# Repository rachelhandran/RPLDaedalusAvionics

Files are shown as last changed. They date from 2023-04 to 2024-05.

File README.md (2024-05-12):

# RPL Daedalus Avionics

5.11.24
Welcome! This is my guide for the RPL Daedalus Project Avionics, in particular, the software and PCB files I designed and used on my rocket during the 2022-2023 cohort.
I used an Arduino Nano to drive 2 sensors, a pressure/altitude/temperature sensor (BMP388), and an IMU/gyroscope/accelerometer/magnetometer (BNO055). The system also includes an SD Card and Module, and a battery. The code written is designed to read pressure/temp/altitude, IMU data, and write it to the SD Card.

The PCB Files are attached, I designed in Eagle. Feel free to copy and edit these files to add or remove any functionalities.

See my latest version and updates below.

## v2/IMUFlightComp.ino
5.20.23 

This is the newest flight computer software that interfaces with the PCB v2.0. It has support for BMP388 temperature, pressure, and altitude sensing, as well as IMU 9DoF Raw Data: Accelerometer, Gyroscope, and Magnetometer data. The software reads all the above data, including IMU calibration status data, and writes them to the SD card in CSV format.

CSV format:
*Temperature (C), Pressure (hPa), Altitude (m), IMU Calibration (System), IMU Calibration (Accelerometer), IMU Calibration (Gyroscope), IMU Calibration (Magnetometer), Accel_X (m/s^2), Accel_Y (m/s^2), Accel_Z (m/s^2), Gyro_X (rad/s), Gyro_Y (rad/s), Gyro_Z(rad/s), Mag_X (uT), Mag_Y (uT), Mag_Z (uT)*

This version of code also supports a Piezo buzzer (but the PCB does not have a spot for the buzzer, this code can only be used on a system designed with a buzzer.) This version plays a constant buzz to inform that data is successfully reading and writing to SD. If not buzzing, the SD Card is likely not initialized properly. Eject and re-enter, and click RESET on the Arduino. Continue until the buzz begins.

## Hardware Setup
5.21.23
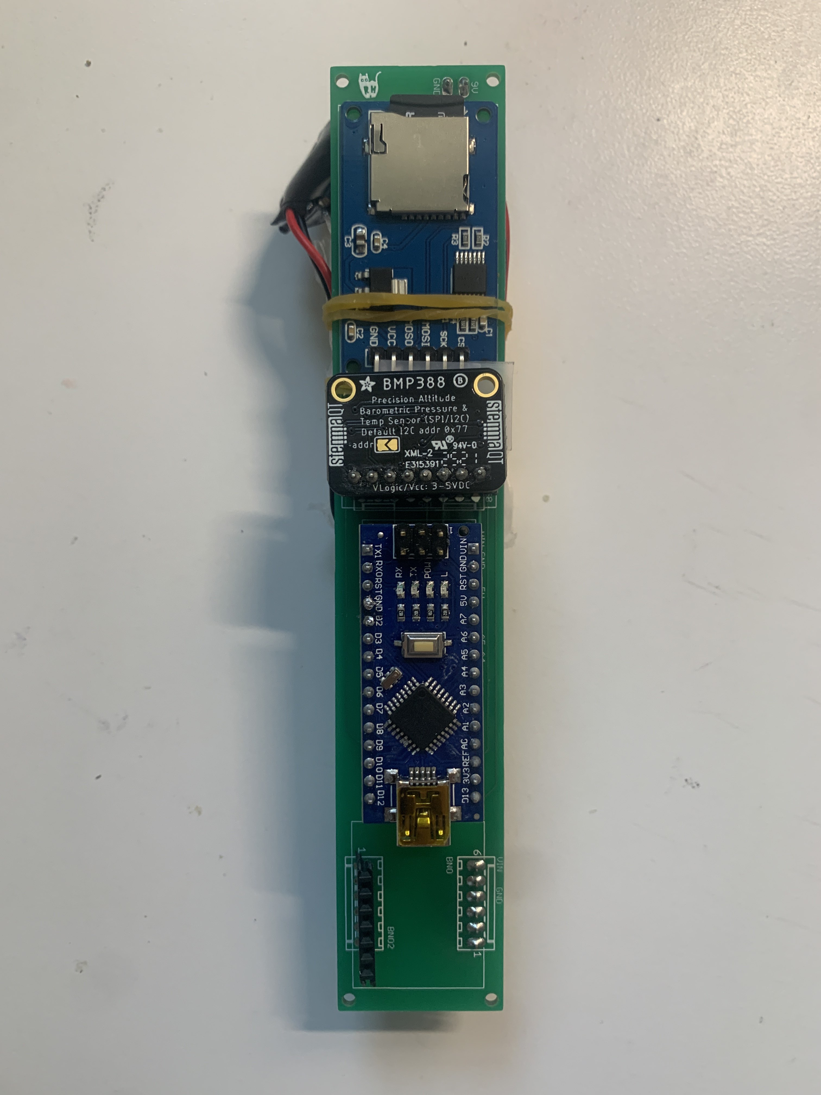
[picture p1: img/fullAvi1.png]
front

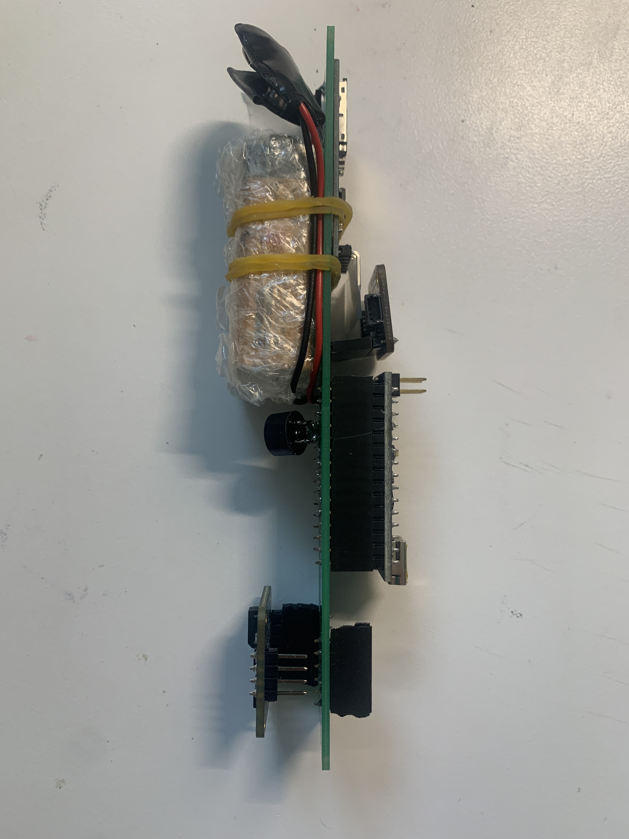
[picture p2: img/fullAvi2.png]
side

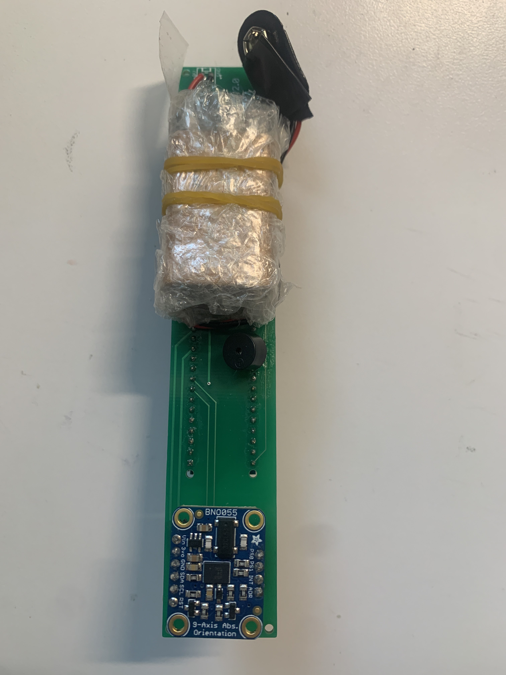
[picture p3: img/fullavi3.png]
back

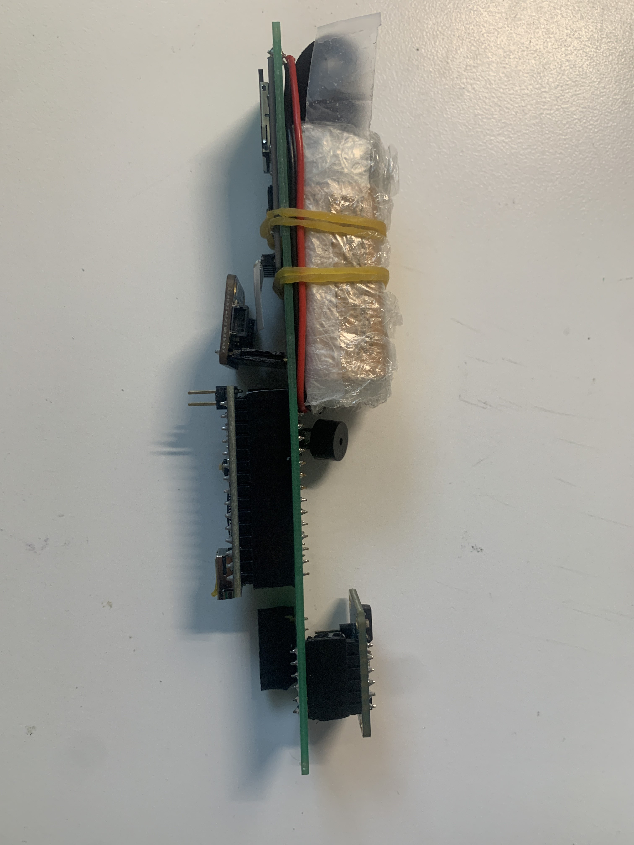
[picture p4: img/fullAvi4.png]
other side


## PCB v2.0
5.6.23

3D Views:
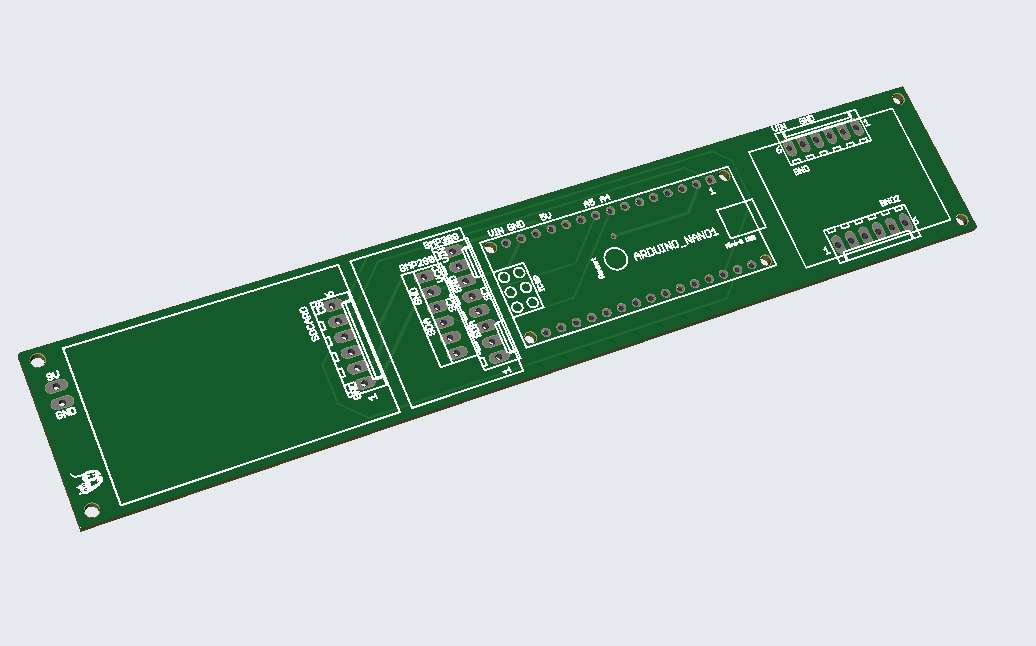
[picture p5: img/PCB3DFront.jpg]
3D Front View

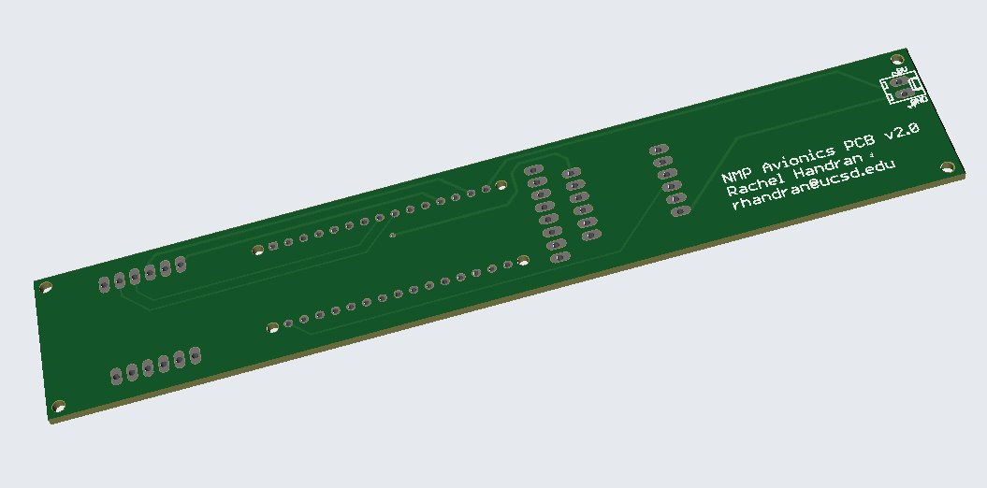
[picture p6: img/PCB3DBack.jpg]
3D Back View


Board: 
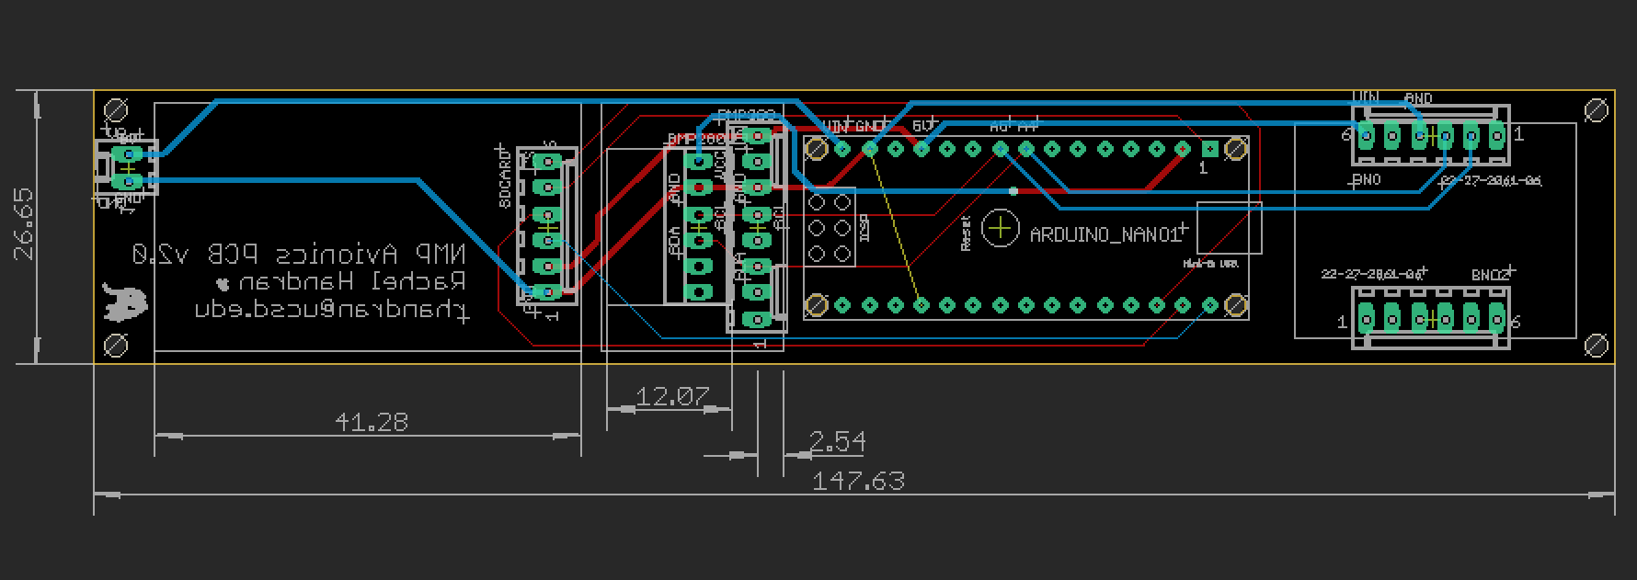
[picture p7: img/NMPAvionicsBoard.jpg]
Board

Schematic: 
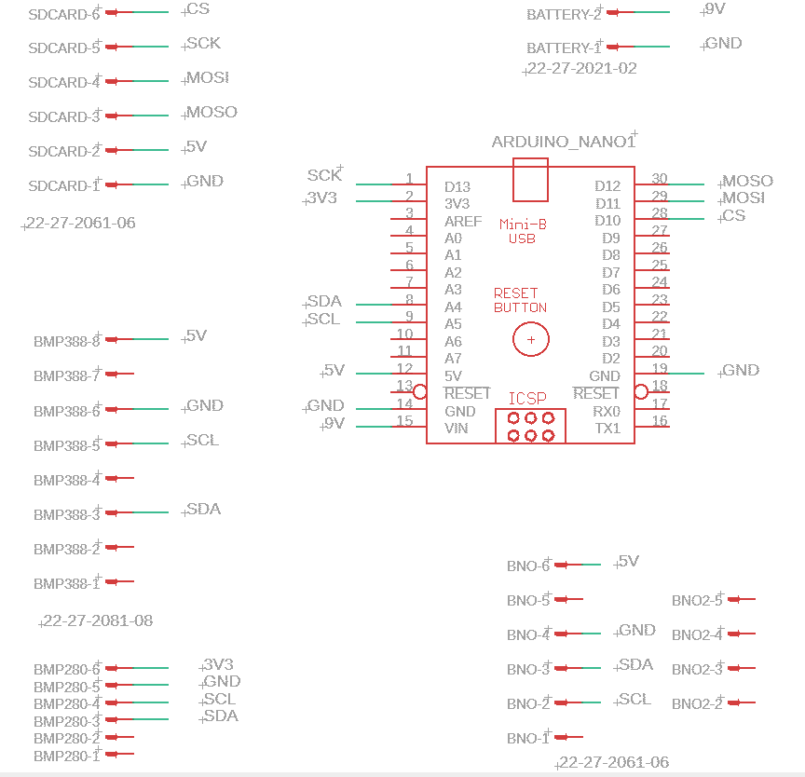
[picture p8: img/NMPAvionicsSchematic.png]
Schematic


## v1.0

This is the flight computer for our NMP Avionics system. 

*The software is designed for BMP388 only. Software is not necessarily compatible for BMP280. Hardware IS compatible with both, but you must write your own code to call the BMP280 library instead of the BMP388.*

`flightComputer.ino` is the flight program. Once uploaded, there will be a 5s delay, then the BMP388 sensor will read in temp, pressure, and altitude data, and write to a file in the SD card once every 100ms.

`flightCompDebug.ino` is outdated. It was a duplicate sandbox code to practice and debug. 

### Hardware/PCB v1 Setup:
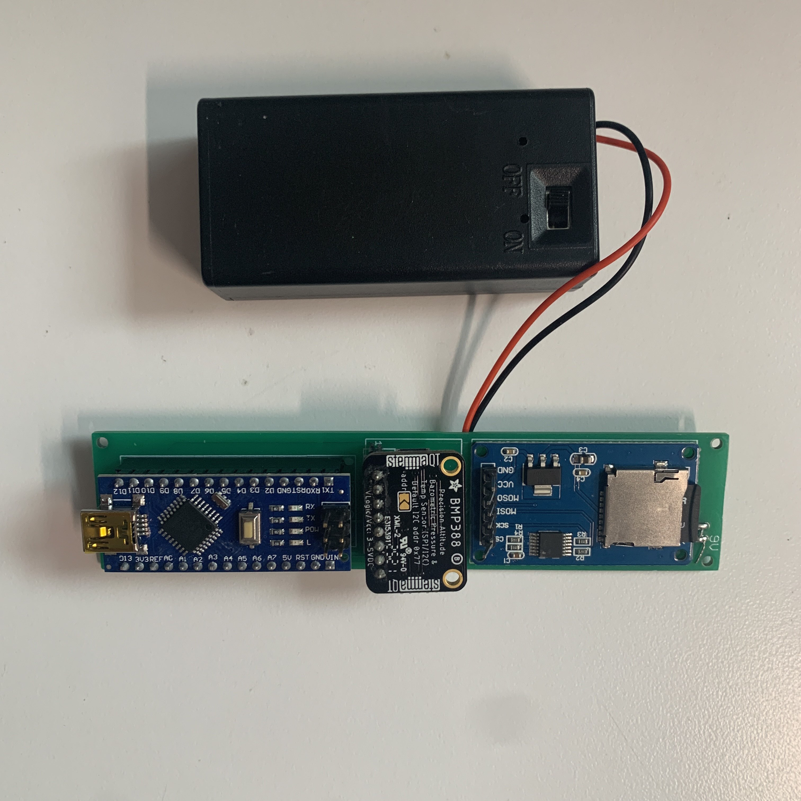
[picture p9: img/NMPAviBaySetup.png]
Avi Setup

Ensure the BMP388 and BMP280 are wired/soldered to the PCB correctly. 
On the PCB, GND is the 2nd pin from the right. Match the GND pin of your component (BMP280) and the GND pin on the PCB when orienting your components to ensure functionality.

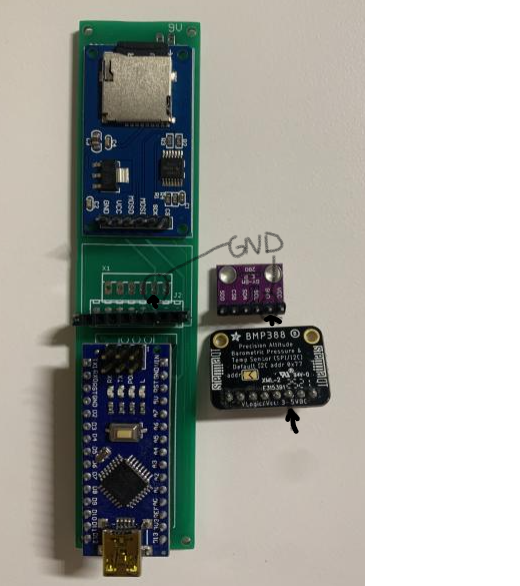
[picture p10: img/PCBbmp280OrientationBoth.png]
PCB

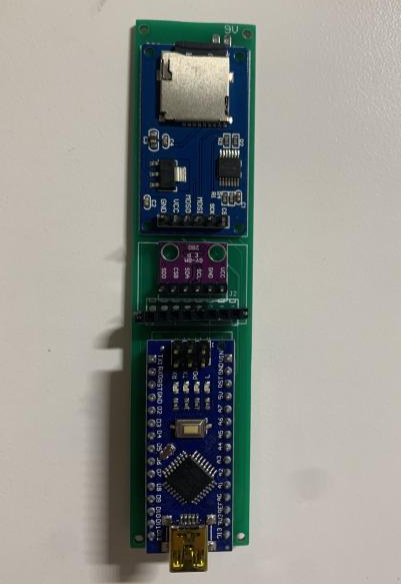
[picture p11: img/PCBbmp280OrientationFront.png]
PCB Front

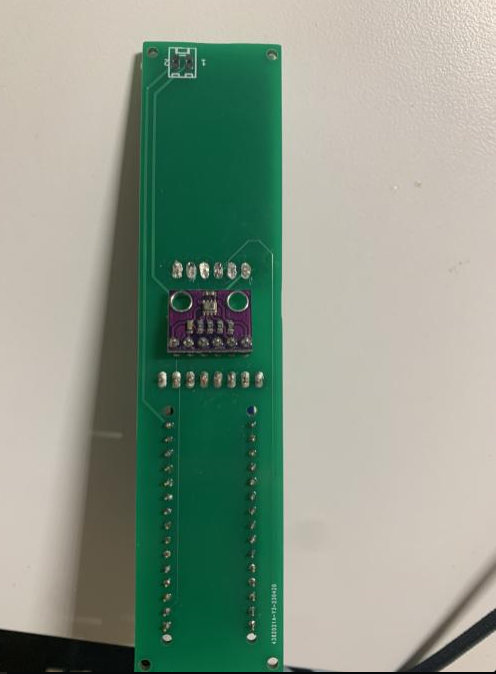
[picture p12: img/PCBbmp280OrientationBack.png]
PCB Back


## Procedure (BMP388 only):
1. Solder PCB components: Arduino Nano, BMP388, SD Card Module, and battery. Ensure you have a new battery. Keep battery OFF. Mount an SD Card.
2. Download flightComputer.ino to your Arduino IDE.
3. Edit flightComputer.ino to Arduino Nano. For testing, ensure number in the filename in line 164 is 100+. If flying, change number to 1-99. This helps for post-processing to distinguish the correct data.
4. Upload your version of flightComputer.ino to the Nano thru USB cable. Check serial monitor to ensure valid output stream. Unplug the cable, now you have successfully uploaded the program and will supply power from now on through the battery pack.
5. Mount the avionics bay in your rocket. When flight time comes, turn on the battery pack. Remember, after 5s, the program will begin. It will end when it loses power or runs out of memory. (Battery goes out much quicker (~10h) than filling up 32GB of storage with plain text, see notes.)
6. Recover the rocket and turn OFF the switch. Read from SD Card for data analysis.

# Notes:
## Memory
How long will it take to fill a 32gb SD card with this data (25 bytes per line)?
- In CSV file, 25 chars = 25 bytes per line
	- 25 bytes / 0.1 second
	- 250 bytes / 1 second
	- 15,000 bytes / 1 min
	- 900,000 bytes / 1 hour
	- 21,600,000 / 24hrs or 1 day
- 32GB = 32,000,000,000 bytes
- It will take 35,555 hours or 1481 days to fill the SD Card at a rate of 25 bytes / sec and 32GB storage

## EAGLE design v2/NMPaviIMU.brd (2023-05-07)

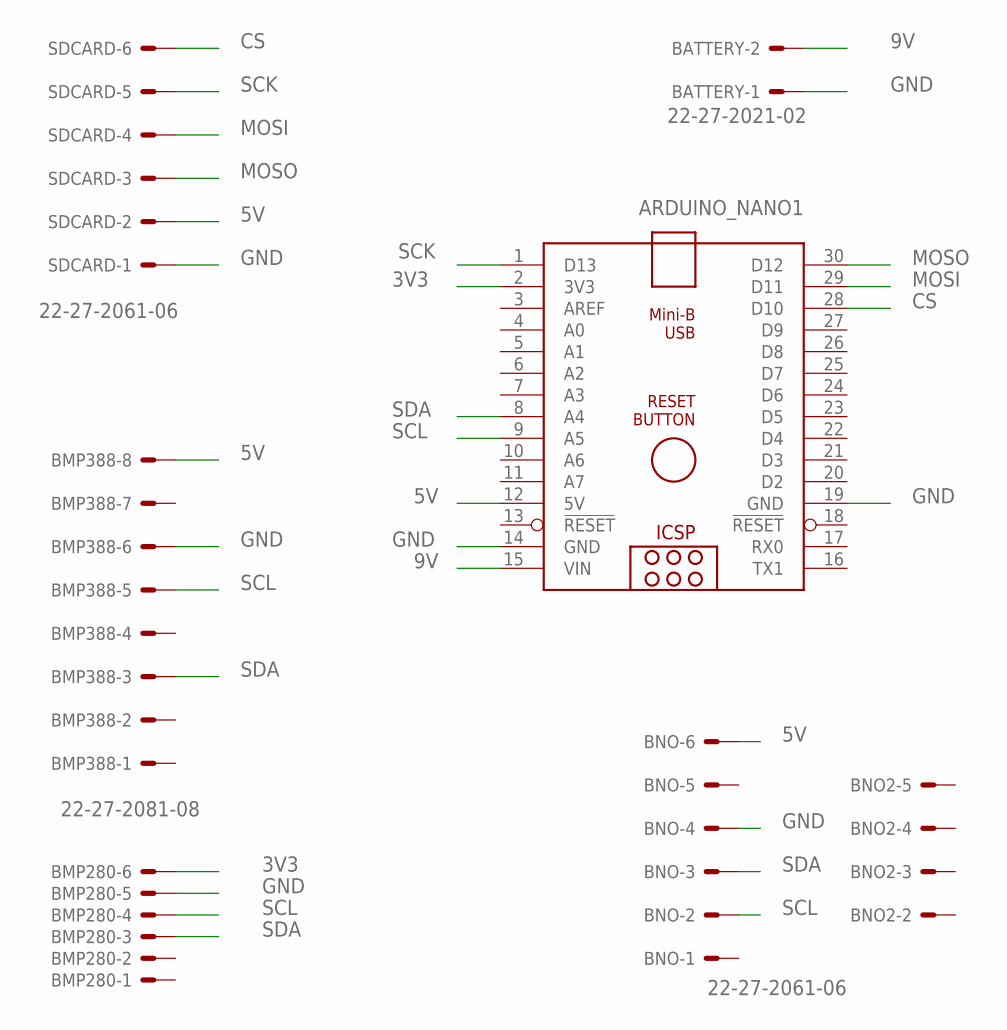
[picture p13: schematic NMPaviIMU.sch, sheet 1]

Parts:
ARDUINO_NANO1: ARDUINO_NANO
BATTERY: 22-27-2021-02; 6410-02
BMP280: 22-23-2061
BMP388: 22-27-2081-08; 6410-08
BNO, BNO2: 22-27-2061-06; 6410-06
SDCARD: 22-27-2061-06; 6410-06

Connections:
3V3: ARDUINO_NANO1.2 (3V3), BMP280.6
5V: ARDUINO_NANO1.12 (5V), BMP388.8, BNO.6, SDCARD.2
9V: ARDUINO_NANO1.15 (VIN), BATTERY.2
CS: ARDUINO_NANO1.28 (D10), SDCARD.6
GND: ARDUINO_NANO1.14 (GND), ARDUINO_NANO1.19 (GND), BATTERY.1, BMP280.5, BMP388.6, BNO.4, SDCARD.1
MOSI: ARDUINO_NANO1.29 (D11), SDCARD.4
MOSO: ARDUINO_NANO1.30 (D12), SDCARD.3
SCK: ARDUINO_NANO1.1 (D13), SDCARD.5
SCL: ARDUINO_NANO1.9 (A5), BMP280.4, BMP388.5, BNO.2
SDA: ARDUINO_NANO1.8 (A4), BMP280.3, BMP388.3, BNO.3

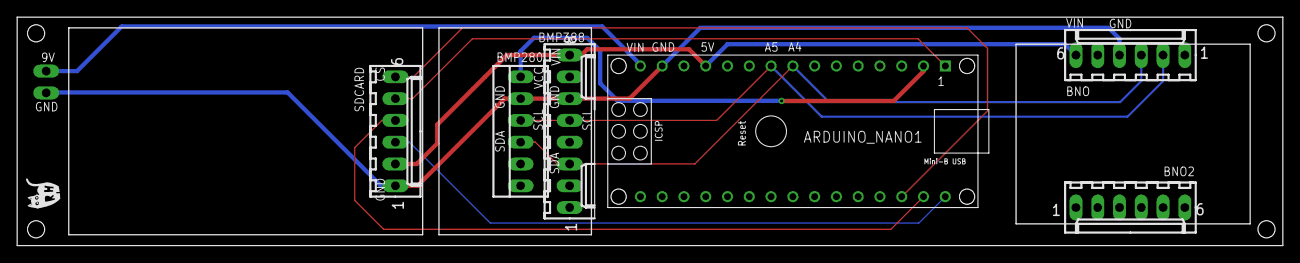
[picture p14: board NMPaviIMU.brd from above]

Board: 2 copper layers, 147.6 x 26.7 mm, 7 parts (1 on the bottom side), 10 nets.

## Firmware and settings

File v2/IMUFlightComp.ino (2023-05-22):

/*
 * Rachel Handran 
 * Flight Computer 5.19.23 with PCB v2.0
 * Current working state: Successfully prints out BMP and IMU calibration and accel, mag, 
 * and gyro data to the serial monitor and writes to a file called on the SD. 
 * 
 * CSV Format: bmp data, imu calibration, then imu raw data
 *    bmp.temp,bmp.pressure,bmp.altitude,system,accel,gyro,mg,acc.x(),acc.y(),acc.z(),gyr.x(),gyr.y(),gyr.z(),mag.x(),mag.y(),mag.z()
*/

#include <Adafruit_Sensor.h>
#include <Adafruit_BNO055.h>  // IMU
#include "Adafruit_BMP3XX.h" // BMP
#include <Wire.h>
#include <utility/imumaths.h>   // IMU
#include <SPI.h>
#include <SD.h>

// Global constants
#define FLIGHT FALSE // TRUE means will only upload the flight info, no serial prints (keep FALSE)
#define IS_DEBUG TRUE // FALSE cancels most print statements, all functions read/write still work
#define IS_DEBUG_BMP FALSE // Keep FALSE
#define DELAY_FIVE (5000)

// BNO Constants
#define BNO055_SAMPLERATE_DELAY_MS (100)

// BMP Constants
#define BMP_SCK 13
#define BMP_MISO 12
#define BMP_MOSI 11
#define BMP_CS 10
#define SEALEVELPRESSURE_HPA (1013.25) // bmp

// Setting up hardware connections
Sd2Card card;
SdVolume volume;
SdFile root;

Adafruit_BMP3XX bmp; // bmp
Adafruit_BNO055 myIMU = Adafruit_BNO055(-1, 0x28, &Wire); // IMU

File myFile;
const int CS = 10;

// Functions

// BMP Functions
void setupBMP() { //bmp
  if (!bmp.begin_I2C(0x77)) {   // hardware I2C mode, can pass in address & alt Wire
    #if IS_DEBUG_BMP
    Serial.println("Could not find a valid BMP3 sensor, check wiring!");
    #endif
    while (1);
  }
  bmp.setTemperatureOversampling(BMP3_OVERSAMPLING_8X);
  bmp.setPressureOversampling(BMP3_OVERSAMPLING_4X);
  bmp.setIIRFilterCoeff(BMP3_IIR_FILTER_COEFF_3);
  bmp.setOutputDataRate(BMP3_ODR_50_HZ);
}

// SD Card Functions
void initialize(){
    #if IS_DEBUG
    Serial.print("Initializing SD card...");
    #endif

  if (!SD.begin(CS)) {
    #if IS_DEBUG
    Serial.println("initialization failed!");
    #endif
    while (1); //stalls the program
  }
  #if IS_DEBUG
  Serial.println("initialization done.");
  #endif
}

// IMU Functions
void setup() {
  // put your setup code here, to run once:
  Serial.begin(115200);
  
  initialize(); //SDcard
  setupBMP(); 
  myIMU.begin();

  int8_t temp = myIMU.getTemp();
  myIMU.setExtCrystalUse(true);
  delay(DELAY_FIVE);
}

void loop() {  
  // put your main code here, to run repeatedly:
  uint8_t sys, gyros, accel, mg = 0;
  myIMU.getCalibration(&sys, &gyros, &accel,&mg);

  imu::Vector<3> acc = myIMU.getVector(Adafruit_BNO055::VECTOR_ACCELEROMETER);
  imu::Vector<3> gyr = myIMU.getVector(Adafruit_BNO055::VECTOR_GYROSCOPE);
  imu::Vector<3> mag = myIMU.getVector(Adafruit_BNO055::VECTOR_MAGNETOMETER);

  /*
  String imu_output = String(accel) + "," + String(gyros)+ "," + String(mg) + "," + String(sys)  + "," + 
      String(acc.x()) + "," + String(acc.y()) + "," + String(acc.z()) + "," + 
      String(gyr.x()) + "," + String(gyr.y()) + "," + String(gyr.z()) + "," +
      String(mag.x()) + "," + String(mag.y()) + "," + String(mag.z()) + ",";
  */

// NEW Development: 5.19.23

#if !FLIGHT
  Serial.println("");
  Serial.print(bmp.temperature);
  Serial.print(",");  
  Serial.print(bmp.pressure/100.0);
  Serial.print(",");  
  Serial.print(bmp.readAltitude(SEALEVELPRESSURE_HPA));
  Serial.print(",");  

  Serial.print(sys);
  Serial.print(",");  
  Serial.print(accel);
  Serial.print(",");  
  Serial.print(gyros);
  Serial.print(",");  
  Serial.print(mg);

  Serial.print(",");  
  Serial.print(acc.x());
  Serial.print(",");  
  Serial.print(acc.y());
  Serial.print(",");  
  Serial.print(acc.z());

  Serial.print(",");  
  Serial.print(gyr.x());
  Serial.print(",");  
  Serial.print(gyr.y());
  Serial.print(",");  
  Serial.print(gyr.z());
  
  Serial.print(",");  
  Serial.print(mag.x());
  Serial.print(",");  
  Serial.print(mag.y());
  Serial.print(",");  
  Serial.print(mag.z());
#endif
  
  // Write to SD Card file

  //Taken from writeFile() function in previoous versions, for testing, copy that original code
  myFile = SD.open("FLIGHT.txt", FILE_WRITE);
 
  myFile.print(bmp.temperature);
  myFile.write(",");
  myFile.print(bmp.pressure/100.0);
  myFile.write(",");
  myFile.print(bmp.readAltitude(SEALEVELPRESSURE_HPA));
  myFile.write(",");

  myFile.print(sys);
  myFile.write(",");
  myFile.print(accel);
  myFile.write(",");
  myFile.print(gyros);
  myFile.write(",");
  myFile.print(mg);
  myFile.write(",");
  
  myFile.print(acc.x());
  myFile.write(",");
  myFile.print(acc.y());
  myFile.write(",");
  myFile.print(acc.z());
  myFile.write(",");

  myFile.print(gyr.x());
  myFile.write(",");
  myFile.print(gyr.y());
  myFile.write(",");
  myFile.print(gyr.z());
  
  myFile.print(mag.x());
  myFile.write(",");
  myFile.print(mag.y());
  myFile.write(",");
  myFile.print(mag.z());
 
  myFile.write("\n");

  myFile.close();
 
  delay(BNO055_SAMPLERATE_DELAY_MS);
}

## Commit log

2023-02-25 v1.0
    Complete working version of NMP flight computer.
    10s delay at start,
    Reads sensor data from BMP388 and stores to SD card every second.
2023-04-18 NMP avionics board, schematic, and gerber files
    [NMPavi280wires.brd, NMPavi280wires.sch]
2023-05-07 uploaded new schematic, brd, gerber files, and updated imgs
    [NMPaviIMU.brd, NMPaviIMU.sch]
2023-05-07 moved files to v1 and v2 folders
    [NMPavi280wires.brd, NMPavi280wires.sch, NMPaviIMU.brd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]
2023-05-20 Update IMUFlightComp.ino
    Printing raw data directly to the SD card. Previous code attempted to convert data into string and print, wich caused problems.
    [IMUFlightComp.ino]
2023-05-20 Update IMUFlightComp.ino
    IMU data prints to serial and SD card in CSV format
2023-05-20 Update IMUFlightComp.ino
    Successful BMP and IMU data to serial monitor AND sd card in CSV format!
2023-05-20 Update IMUFlightComp.ino
    Deleted unnecessary helper functions.
2023-05-20 Update IMUFlightComp.ino
    Added piezo buzzer
    [IMUFlightComp.ino]
2023-05-21 Update IMUFlightComp.ino
    Added debug if statement
2023-05-22 Revert IMUFlightComp.ino to no buzzer
    No buzzer
    [IMUFlightComp.ino]
